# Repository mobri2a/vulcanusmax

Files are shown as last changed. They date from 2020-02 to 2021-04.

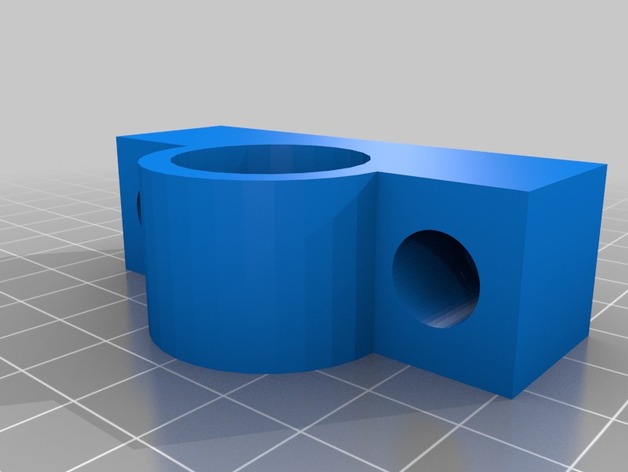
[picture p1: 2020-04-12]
Printed Parts/images/Z_bearing_holder_preview_featured.jpg

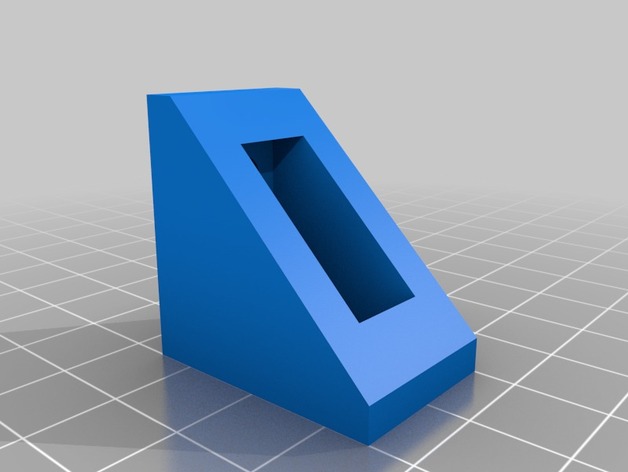
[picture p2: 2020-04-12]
Printed Parts/images/CoreXY_Corner_Bracket_2020_preview_featured.jpg

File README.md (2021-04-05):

# Vulcanus Max

This is the definitive repository for config files for this printer. Firmware is not stored here!

Vulcanus Max is an open source CoreXY, large-capacity printer:
* 2020 extrusion frame
* NEMA 17 stepper motors
	* Kysan 1124090: 1.5A, 4.2V, 1.8 deg
	* Bondtech Extruder
* BigTree Tech SKR v1.4 (LPC1768-based)
* BigTree Tech TFT35 V3.0 Graphic Smart Display Controller https://smile.amazon.com/gp/product/B07VWF4W3J/ref=ppx_yo_dt_b_search_asin_title?ie=UTF8&psc=1
* TMC2209 Drivers
	* Sensorless homing (X&Y)
* BuildTak flexible build plate
* Dual E3D V6 hot ends
* Type 1 thermistor: HT-NTC100K 3950

# Configure and Build Marlin

* Use VSCode. 
* Download latest Marlin, if you so choose.
* Copy latest config from source/Marlin in this repo. 
	* Note: often best to transfer values to new config so as to be up to date on Marlin parameters.

## PINDA Probe Wiring

Connect to Z-MIN. Note: Vulcanus is wired to the Probe and Sensor, which is entirely unnecessary and should be changed to Z-MIN (2/28/21)
bl red green black
+---+
  . | ----- +5V ----- Black -------- Brown
| . | ----- SIG ----- Red   -------- Black 
  . | ----- GND ----- Green -------- Blue 
+---+    

### Pinda wires

* W - not used (temperature sensor on Prusa printers)
* Black - SIG      
* Blue - GND
* Brown - +5V

## Wifi Support

If connecting for the first time, stop looking all over the internet and worrying with that silly BTT Writer. Look at available WiFi SIDs. 

1) Connect to ESP3D. 
2) Go to 192.168.0.1
3) Upload index.html.gz
4) Reboot the printer
5) Go to 192.168.0.1
6) Follow the setup instructions

After initial configuration you'll need to reboot the printer to get the DHCP address from the display. Navigate to that IP and continue setup.

7) Change Station IP Mode to Static
8) Set an IP address (use OctoPi + 1)
9) Set gateway IP
10) Reboot the printer when done and verify static IP address is set

## Embedded WebUI

First time you will need to upload index.html.gz. Get it from https://github.com/luc-github/ESP3D-WEBUI. Use the default UI to upload it, then reboot.

## Notes

**Extruder**: Do not exceed 30mm/s extraction speed. It's a geared extruder and it *does not like it.*

# Build

* Build with PlatformIO. Easiest to output to SD Card

# Install

* Put the MicroSD card from **Build** in the printer and power off/on.
* Reset the EEPROM stored settings: M502, M500, M501

# Operate

## UBL

**Flex Plate**: UBL works very well with the BuildTak flexible build plate system. A script has been configured on Octopi for this purpose.

**Note on Sensorless Probing:** I read that it's not that accurate enough on the Z-axis. TMC2209 on the E0, E1, and Z axis have Stallguard diagnostic pins removed.

Latest: 2/28/21

```
;------------------------------------------
;--- Setup and initial probing commands ---
;------------------------------------------
;M502            ; Reset settings to configuration defaults...
;M500            ; ...and Save to EEPROM. Use this on a new install.
;M501            ; Read back in the saved EEPROM.
M117 UBL Bed Leveling...
M140 S{{ parameters.bedtemp }}          ; Not required, but having the printer at temperature helps accuracy
M109 S{{ parameters.extrudertemp }}     ; Not required, but having the printer at temperature helps accuracy
M190 S{{ parameters.bedtemp }}          ; Wait for the bed (if not already at temperature)

G28             ; Home XYZ.
M155 S30        ; reduce temperature reporting rate
G29 P1 T        ; Do automated probing of the bed.
;G29 P2 B T      ; Manual probing of locations USUALLY NOT NEEDED!!!!
G29 P3 T        ; Repeat until all mesh points are filled in.

#G29 T           ; View the Z compensation values.
G29 S{{ parameters.slot }} ; Save UBL mesh points to EEPROM.
G29 F{{ parameters.fade }}; Set Fade Height for correction at 10.0 mm.
G29 A           ; Activate the UBL System.
@BEDLEVELVISUALIZER     ; tell plugin to watch for reported mesh
M420 S1 V
M500            ; Save current setup. WARNING: UBL will be active at power up, before any `G28`.
;---------------------------------------------
;--- Fine Tuning of the mesh happens below ---
;---------------------------------------------
;G26 C P5.0 F3.0 ; Produce mesh validation pattern with primed nozzle (5mm) and filament diameter 3mm
                ; PLA temperatures are assumed unless you specify, e.g., B 105 H 225 for ABS Plastic
;G29 P4 T        ; Move nozzle to 'bad' areas and fine tune the values if needed
                ; Repeat G26 and G29 P4 T  commands as needed.

;G29 S1          ; Save UBL mesh values to EEPROM.
;M500            ; Resave UBL's state information.
;----------------------------------------------------
;--- Use 3-point probe to transform a stored mesh ---
;----------------------------------------------------
;G29 L1          ; Load the mesh stored in slot 1 (from G29 S1)
;G29 J           ; No size specified on the J option tells G29 to probe the specified 3 points
                ; and tilt the mesh according to what it finds.

M104 S0
M140 S0
M155 S30		; reset temperature keepalive
```

### Setup

#### Do this any time a change is made to the build surface that could change its contour. Run the script above manually, or use the custom command in Octopi.

#### Step 2 - Glass beds

Manually adjust every point on the mesh with a feeler gauge. From the clickwheel, find the menu item to adjust every mesh point. Adjust each to consistent clearance.

#### Step 3

Optional: Get the mesh, load it into Excel, and create a 3D graph of the surface.

1. Copy/paste the mesh data from G29 T
2. Paste into Excel (see file in this repo)
3. Data->Text to columns. Take defaults
4. Delete columns 1 and 3
5. Select data cells and sort by column A (gets rid of blanks and orients graph to match front right view of the bed)
6. Create a 3D Line Chart of the bed measurements

UBL Bed Topology Visualized as an Excel 3D Line Chart

## Bilinear Bed Leveling
### Procedure
1) Preheat for PLA. Heaters (bed and hot end) should remain on. Let the bed fully soak in the heat for a few minutes
2) Use the menu to execute Bed Leveling (I think this is G29)
3) Make sure Bed Leveling is ON

## Adjustments
### Z Offset
* Adjust it before you print
* ...or double-click the knob **during** print and adjust (head adjusts as you turn the knob)
# Contents of this Repo

## source/Marlin

Contains Marlin configs.

### To Update Marlin

* download a zip of the latest Marlin firmware
* Copy the file platformio.ini to the root (same level as Marlin, docs, data, lib, etc)
* Copy the latest configs to the Marlin folder within the downloaded repo
* Build using VSCode

**Note**: It's better to transcribe your config, editing the latest Marlin version to match. Often config directives change between releases. Same for platformio.

Latest build is in Documents/Marlin/Marlin-bugfix-2.0.x, built 4/23/2020. I was attempting to make UBL work properly. It didn't. See open issue on GitHub. Working currently on adding WiFi support.

WiFi is enabled on Serial 1

### See:
* http://www.github.com/codiac2600

## Cura

All files needed to install the printer into Cura

## Other

printer_init.gcode - sets up the unified bed leveling mesh

# Specifications

https://mak3r.de/2020/04/03/stepper-driver-current-and-vref-calculator/

## X Axis

Stepper motor: Kysan 1124090 Nema 17
2 Phase
1.8 angle
2.8ohm / phase
1.5A / phase
5mm

RMS = 1.5 / 1.41 = 1.064
Vref = (1.064 * 2.5) / 1.77 = 1.502
90% = 1.5 = 958mA

Driver: TMC2209 in UART mode with StallGuard

Pulley: GT2 20 tooth

Belt pitch: 2mm

## Y Axis

Stepper motor: Kysan 1124090 Nema 17
2 Phase
1.8 angle
2.8ohm / phase
1.5A / phase
5mm

RMS = 1.5 / 1.41 = 1.064
Vref = (1.064 * 2.5) / 1.77 = 1.502
90% = 1.5 = 958mA

Driver: TMC2209 in UART mode with StallGuard

Pulley: GT2 20 tooth

Belt pitch: 2mm

## Z Axis

Stepper motor: Kysan 1124090 Nema 17 (2)
2 Phase
1.8 angle
2.8ohm / phase
1.5A / phase
5mm

RMS = 2 * 1.5 / 1.41 = 2.128
Vref = (2.128 * 2.5) / 1.77 = 3.006
90% = 1.9152 = 1915mA

RMS: Conservatively set X_CURRENT to 1500 (2/28/21)

Driver: TMC2209 in UART mode

Min Z Probe: 18mm inductive

Lead screw: 8mm

## Extruder 1

Stepper motor: Bondtech 42H025H-0704-002 25mm NEMA 17 0.7A, 2.9V, 1.8 deg
2 Phase
1.8 angle
4.2ohm / phase
0.7A / phase
2.9V / phase

Driver: TMC2209 in UART mode

RMS = 0.7 / 1.41 = 0.496
Vref = (0.496 * 2.5) / 1.77 = 0.700 V
90% = 0.496 = 446mA

## VREF Calculation

RMS current = Max current / 1.41
Vref = (RMS Current x 2.5) / 1.77
Use 90% of RMS current

----- old stuff----
# Vulcanus Max
## Overview

This project is to create a large-format 300x300x400mm Fused Deposit Modelling (FDM) printer based on CoreXY design using the 2015 Vulcanus Max project as a starting point.

## Configure and Build Marlin

1) Download BTT Marlin 2.0.x bugfix
2) Download latest 2.0 Marlin
3) Copy #2 over #1
4) Copy platformio.ini to root of #1 over the exiting platformio.ini
5) Edit the config files in #1 and transfer settings from latest build/Marlin in this repo

### Specific Config Changes

#### configuration.h

Numerous (to be listed)

```
#define STRING_CONFIG_H_AUTHOR "(Elvantech, SKR-V1.4 LPC1768)"
#define SERIAL_PORT 3
#define SERIAL_PORT -1
#define BAUDRATE 115200
#define MOTHERBOARD BOARD_BTT_SKR_V1_4
#define CUSTOM_MACHINE_NAME "Vulcanus SKR"
#define REPRAP_DISCOUNT_FULL_GRAPHIC_SMART_CONTROLLER
#define NEOPIXEL_LED
  #define NEOPIXEL_TYPE   NEO_GRB 
  #define NEOPIXEL_PIN     P1_24  
  #define NEOPIXEL_PIXELS 26    
  #define NEOPIXEL_STARTUP_TEST 
```
Preheats
```
#define PREHEAT_1_LABEL       "PLA"
#define PREHEAT_1_TEMP_HOTEND 210
#define PREHEAT_1_TEMP_BED     60
#define PREHEAT_1_FAN_SPEED     0 // Value from 0 to 255

#define PREHEAT_2_LABEL       "ABS"
#define PREHEAT_2_TEMP_HOTEND 245
#define PREHEAT_2_TEMP_BED    105
#define PREHEAT_2_FAN_SPEED     0 // Value from 0 to 255

#define PREHEAT_3_LABEL       "Nylon"
#define PREHEAT_3_TEMP_HOTEND 245
#define PREHEAT_3_TEMP_BED     80
#define PREHEAT_3_FAN_SPEED     0 // Value from 0 to 255

#define PREHEAT_4_LABEL       "PETG"
#define PREHEAT_4_TEMP_HOTEND 230
#define PREHEAT_4_TEMP_BED     70
#define PREHEAT_4_FAN_SPEED     0 // Value from 0 to 255

#define PREHEAT_5_LABEL       "TPU"
#define PREHEAT_5_TEMP_HOTEND 200
#define PREHEAT_5_TEMP_BED     90
#define PREHEAT_5_FAN_SPEED     0 // Value from 0 to 255
```

#### configuration_adv.h

X_CURRENT = 1000
Y_CURRENT = 1000
Z_CURRENT = 1000

#### configuration_secure.h

Just copy it.

## Objectives

### Features

* Remote printing

Use OctoPrint to print over WiFi. The built-in camera lets you monitor your print. OctoPrint allows you to remotely control the printer.

* Heated Bed

The build surface can use the Monoprice 300x300 flexible build plate or borosilicate glass plate. Autoleveling makes print setup easier.

* Zoned Heated Bed

The 300x300mm heated bed has 3 zones, small, medium, or large, to reduce power consumption by only heating the portion of the bed that is needed based on the footprint of the model.

* Controller

32 bit processor running at 120MHz with 2209 stepper motor drivers and Marlin 2.0 firmware.

* Extruders

Dual Bowden tube extruders minimize print head mass for less vibration and faster print head movement.

* Vibration-free Frame

Dampers are used on all moving parts to reduce vibration.

* Ambient Temperature Management

Insulated side panels and an exhaust fan allow control of the ambient temperature inside the printer. A heater brings the enclosure quickly up to temperature before your print starts.

* Safety

High amperage power is isolated and protected so that an electrical fault will not cause a fire or damage to the controller.

## Design

### Frame

### Lighting

### Gantry

### Heated Bed

### Print Head

#### Hot Ends

#### Extruders

### Controller

32 bit BIGTREETECH

#### Firmware

Marlin 2.0

### Power

## Bill of Materials

| Item | Qty | Cost |
| -- | :--: | --: |
| [BIGTREETECH TMC2209 V1.2 Stepper Motor Drivers](https://www.aliexpress.com/snapshot/0.html?productId=33029587820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)| 5 | $28.88 |
| [BIGTREETECH SKR V1.4 Turbo Control Board](https://www.aliexpress.com/snapshot/0.html?productId=4000480059509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)| 1 | $33.00 |
| Stepper Motors | | |
| 2020 Extrusion | | |
| Display panel | | |
| Extruder | | |
| Hot End | | |

## Printed Parts

## References

### Similar projects

* [Vulcanus MAX](https://www.instructables.com/id/Vulcanus-MAX-CoreXY-Aluminum-Frame-RepRap-3D-Print/)
* [Vulcanus V1](https://www.instructables.com/id/Vulcanus-V1-3D-Printer/)

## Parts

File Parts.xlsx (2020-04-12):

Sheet: Sheet1
2020 Extrusion | https://www.aliexpress.com/item/32859762475.html
2020 Extrusion | https://www.aliexpress.com/item/32918828145.html

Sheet: Budget
Part | Description/Notes | Qty | Budget | Actual | Link/Order

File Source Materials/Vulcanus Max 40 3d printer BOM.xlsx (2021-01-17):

Qty | Part Name/Type | Source | Source Qty | Source Price
 | FRAME |  |  |  | ordered 3/30 | Status
4 | 20x20 Aluminum Extrusion - 700mm - 5537T101 | https://folgertech.com/products/2020-20mm-x-20mm-x-1meter-extruded-alumium-beam-for-kossel-diy-projects | 4 | $30.33 total | aliexpress
16 | 20x20 Aluminum Extrusion - 590mm length |  | 10 @ 1200 |  | banggood
2 | 20x20 Aluminum Extrusion - 505mm length
2 | 20x20 Aluminum Extrusion - 460mm length
1 | 20x20 Aluminum Extrustion - 600mm | for x carriage | 1 | $12.95 | aliexpress | Received
1 | 20x20 Aluminum Extrusion - 590mm length - x carriage (NEW)
 | 24 pieces @ 1meter long |  | Total | $107.76 + 40.35 shipping
4 | 12mm smooth rods - 541mm length | http://www.ebay.com/itm/162021393198?var=460991532709 | 4 | $16.57 + $5.57 shipping | aliexpress | Reordered | 2020-06-27
 | Replaced with linear rails for x and y axis
4 | Linear rails 600mm | https://www.aliexpress.com/item/33013832781.html |  | $22.73 | aliexpress
2 | 10mm smooth rods - 537mm length | http://www.ebay.com/itm/152032174444?var=451230323416 | 4 pcs @ 600mm | $16.83 | aliexpress | Received
2 | 10mm smooth rods - 511mm length |  |  |  |  | Received
160 | M5 extrusion nuts | https://folgertech.com/products/12-x-lm8uu-4-x-608zz-2-x-623zz-bearing-kit-prusa-i3-rework-reprap-3d-printer | 100pcs | $12.99 + shipping | banggood | received
120 | M5 - 10mm screws | http://www.ebay.com/itm/262320320195?var=561086661523 | 50 pcs | $4.19 | banggood | out of stock
30 | M5 - 12mm screws | http://www.ebay.com/itm/262320320195?var=561086661523 | 50 | $4.39 | banggood | out of stock
8 | M5 - 25mm screws | http://www.ebay.com/itm/262320320195?var=561086661523 | 10 | $3.99 | banggood | out of stock
2 | M8 screw rods - 31.5cm -400m stock with brass nut | https://folgertech.com/products/400mm-lead-screw-3d-printer-z-axis-lead-screw-acme-lead-screw-8mm-screw-pitch | 1 | $15.99 | aliexpress |  |  | order running late - reordering
100 | M4 square nuts | http://www.ebay.com/itm/262161161642?var=560925921904 | 100 | $8.49 | aliexpress
100 | M4 screw - 6mm | http://www.ebay.com/itm/Metric-M3-M4-Black-10-9-Alloy-Steel-Button-Head-Hex-Socket-Cap-Screw-Bolt-/222066527965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 | 50 | $2.65 | aliexpress
 | m4 hex nuts | http://www.ebay.com/itm/131660048805?var=431050278100 | 50 | $2.65
8 | LM10UU linear bearings | https://folgertech.com/products/10x-lm10uu-linear-bearing | 8 | 2 for $3.68 | aliexpress
4 | LMK12L linear bearings | http://www.ebay.com/itm/162014356405 | 1 | $7.82 for 2 + $3.23 shipping | aliexpress | Reordered | 44009
 | Replaced with linear rails for x and y axis
17 | 624 bearings | http://www.ebay.com/itm/310578391085 | 5pcs | 4 @ $13.80 | aliexpress
2 + 2 | GT2 pulleys and belts | http://www.ebay.com/itm/291658850152 | 8 + 5 | $11.92 + $2.99 shipping | banggood
1 | MK8 Direct Drive Gear for Extruder | http://www.ebay.com/itm/201531284546 | 2 | $5.99
2 | M8 threaded rod - 31.5cm length | http://www.ebay.com/itm/322101241224?var=511026880397 | 1 | $8.59 + $1.85
2 | Z axis 5mm to 8mm coupler | http://www.ebay.com/itm/221500601581 | 2 | $3.96 | banggood | received
1 | 5mm x 500mm x 500mm aluminum plate |  |  |  |  | redesign - I don't like how the Vulcanus uses a 5mm plate to support a 5mm plate
1 | 5mm x 400mm x 400mm aluminum plate |  |  |  | aliexpress | received
 | 8mm anti-backlash spring-loaded nut |  | 2 | 2.29 | banggood | out of stock
 | ELECTRONICS
5 | Nema 17 Stepper Motor Bipolar | http://www.ebay.com/itm/231427537485 | 5 | $58.00
1 | Ramps 1.4 kit w/Arduino Mega 2560 & LCD, stepper motor drivers | http://www.ebay.com/itm/321977486681 | 1 | $39.90 + $3.58 shipping | N/A
1 | E3D V6 hotend 1.75mm | https://www.matterhackers.com/store/printer-accessories/v6-hotend-full-kit-1.75mm-universal | 1 | $78.00 | N/A
3 | Scythe Mini KAZE ULTRA 40mm Silent Mini Fan | http://www.ebay.com/itm/162119217575 | 1 | $6.09 | banggood | received
2 | SilenX EFX-08-12 80mm Effizio Quiet Case Fan | http://www.ebay.com/itm/291286908487 | 1 | $8.99 | banggood
1 | 40cm x 40cm 600W 110V Silicone Heater Pad | http://de.aliexpress.com/item/Silicone-Heating-Pad-Heater-110V-600W-400-400mm-for-3d-printer-heat-bed/32639533112.html | 1 | $32 + $21.08 | banggood | received
1 | EVGA 210-GQ-1000-V1 1000W ATX12V / EPS12V Power Supply | http://www.newegg.com/Product/Product.aspx?item=N82E16817438062 | 1 | $129.99 |  | Need to figure out power needs. Would like to use 24V PS
5 | TMC2209 stepper driver |  |  |  | banggood | out of stock
 |  |  | ebay total | $301.85
 |  |  | Folgertech | $215.92
 |  |  | matter hackers | $78.00
 |  |  | ali express | $53.08
 |  |  | newegg | $129.99
 |  |  | TOTAL as of 8/3/16 | $778.84
 |  |  | KEY:
 |  |  | Needs update
 |  |  | Purchased

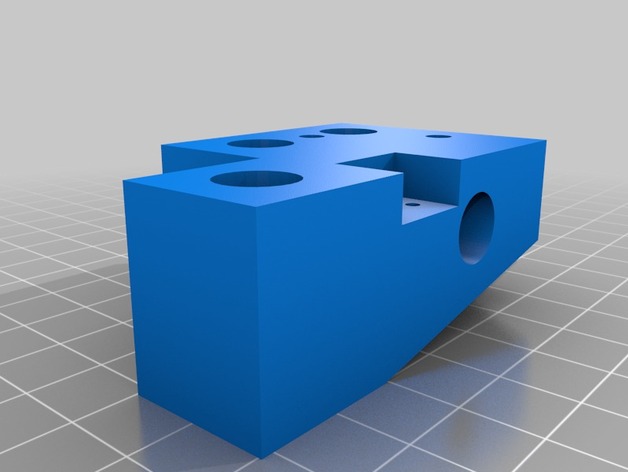
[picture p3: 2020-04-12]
Printed Parts/images/YidlerRight_preview_featured.jpg

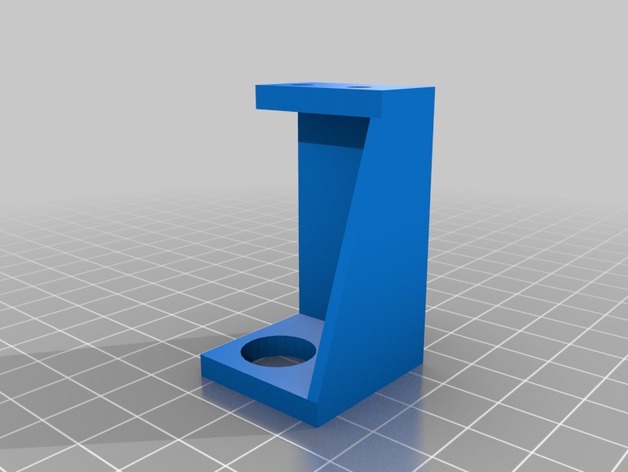
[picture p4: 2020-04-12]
Printed Parts/images/05fd83058f6de9fed415d9ea554de397_preview_featured.jpg

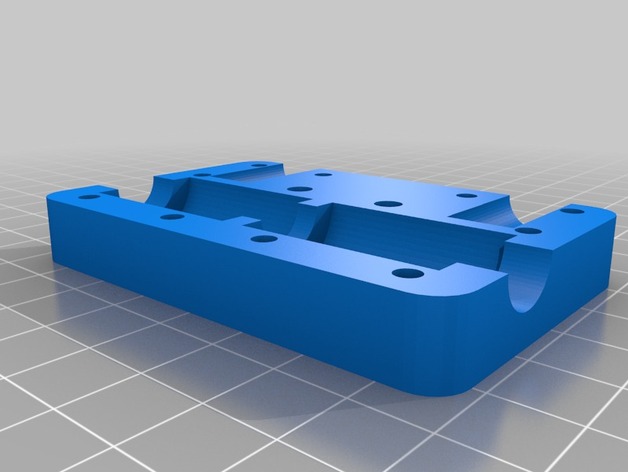
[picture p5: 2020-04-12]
Printed Parts/images/XRightdown_preview_featured.jpg

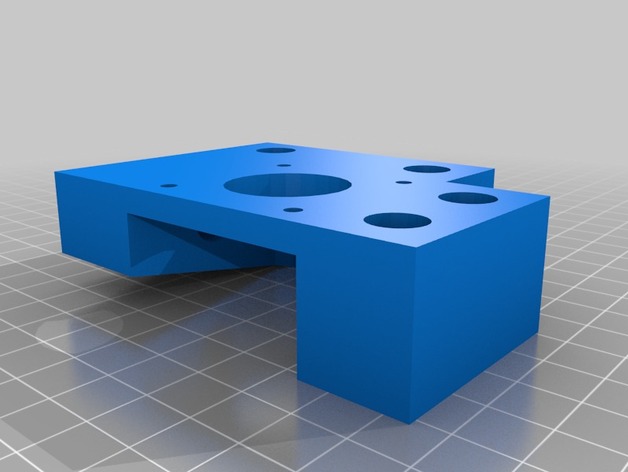
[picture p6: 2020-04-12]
Printed Parts/images/e0d60139beee853cb4de93a20eb8b1da_preview_featured.jpg

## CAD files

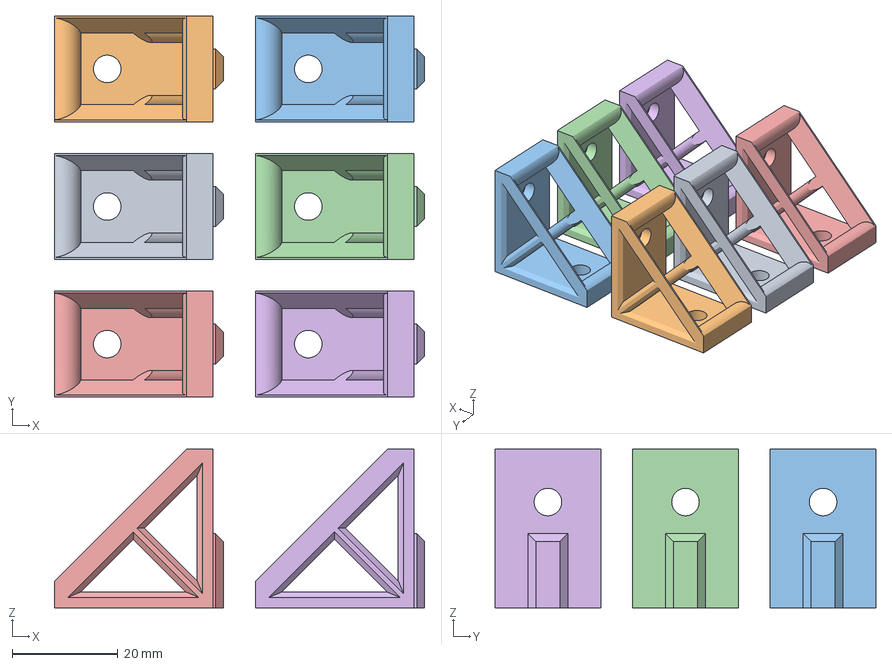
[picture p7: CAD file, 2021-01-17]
Printed Parts/files/corner-bracket-ebt.3mf
70.0 x 72.0 x 30.0 mm

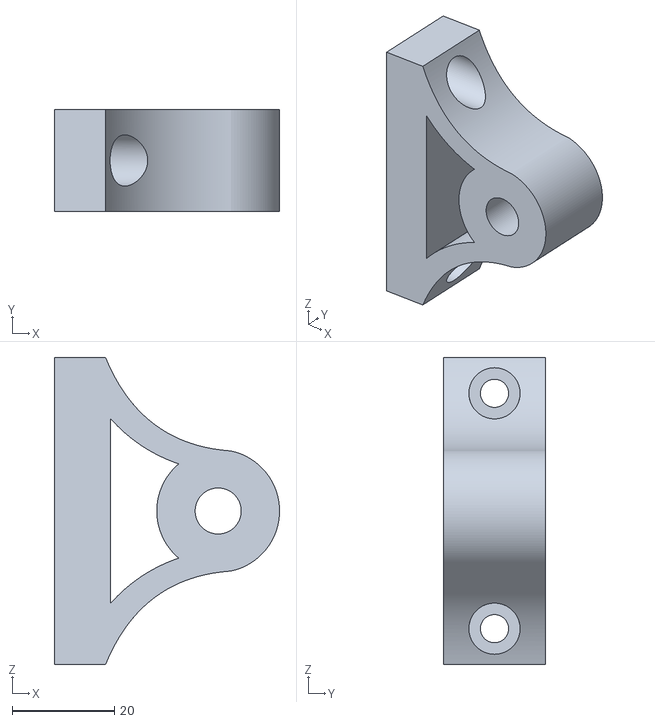
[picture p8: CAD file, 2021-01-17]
Printed Parts/files/z-block-ebt.stl
44.0 x 20.0 x 60.0

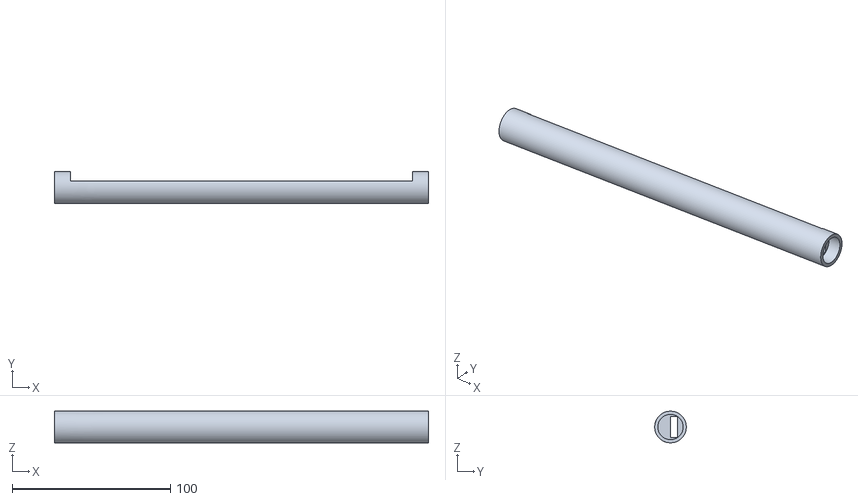
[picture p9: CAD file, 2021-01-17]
Printed Parts/files/lightbar.stl
236.0 x 20.0 x 20.0

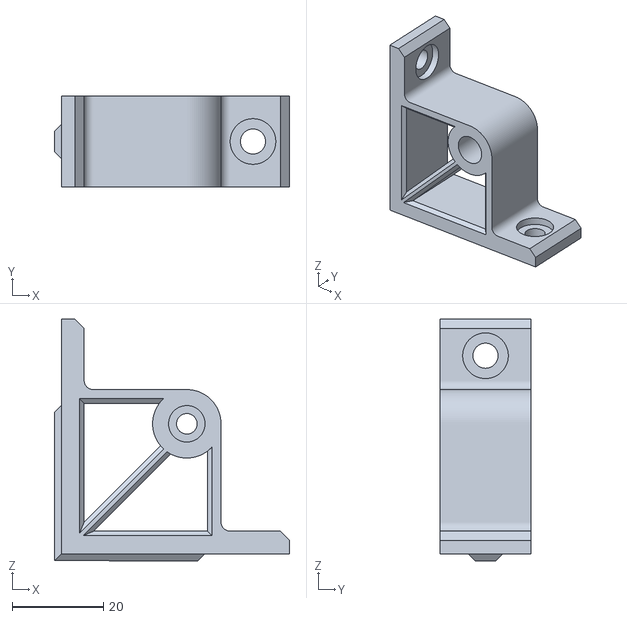
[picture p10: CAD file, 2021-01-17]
Printed Parts/files/bed corner 1.stl
51.5 x 20.0 x 52.9

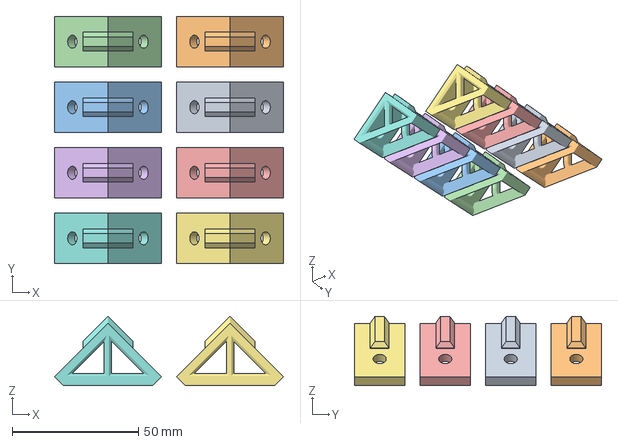
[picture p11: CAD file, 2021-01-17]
Printed Parts/files/corner-bracket-ebtx8.3mf
90.9 x 98.0 x 27.6 mm

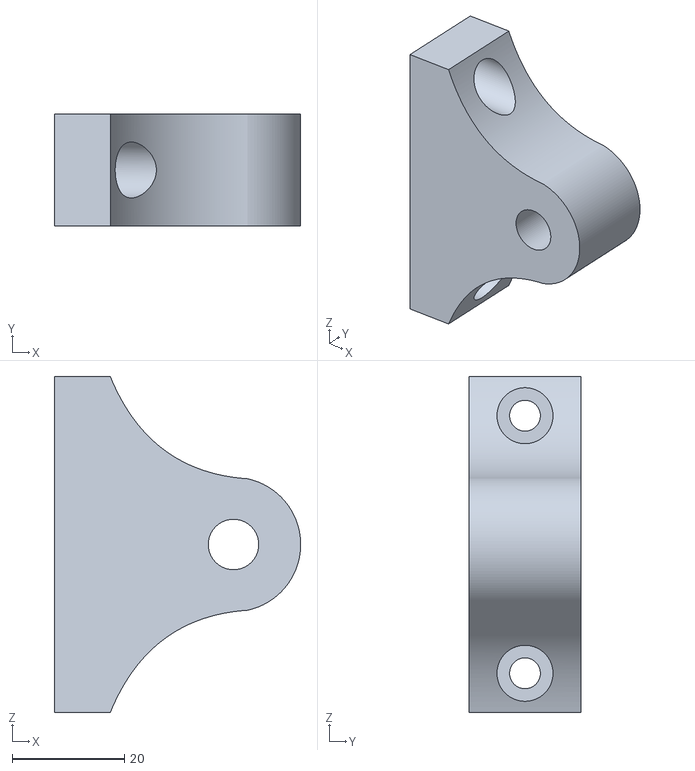
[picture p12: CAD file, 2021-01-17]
Printed Parts/files/z-axis-vm.stl
44.0 x 20.0 x 60.0

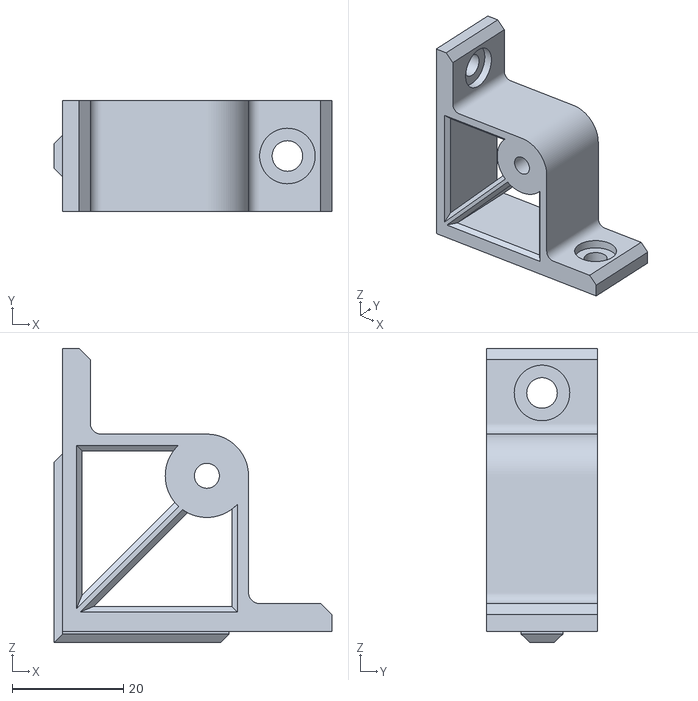
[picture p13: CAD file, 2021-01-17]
Printed Parts/files/bed corner 2.stl
50.0 x 20.0 x 52.9

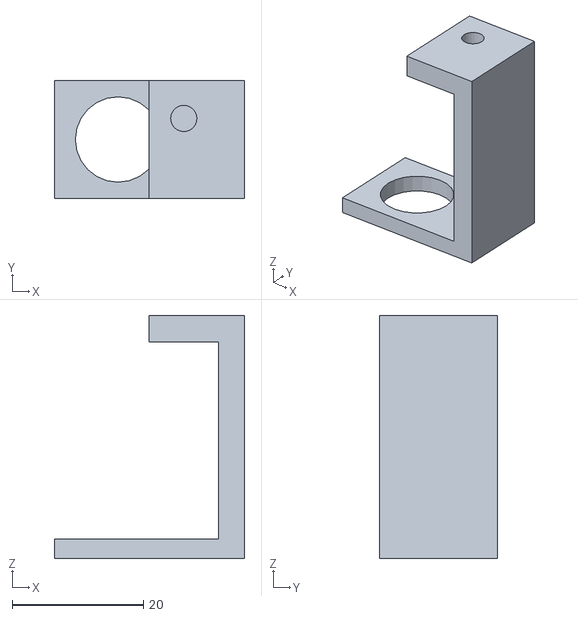
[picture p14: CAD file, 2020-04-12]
Printed Parts/files/Inductive_sensor_holder_fixed.stl
29.0 x 18.0 x 37.0

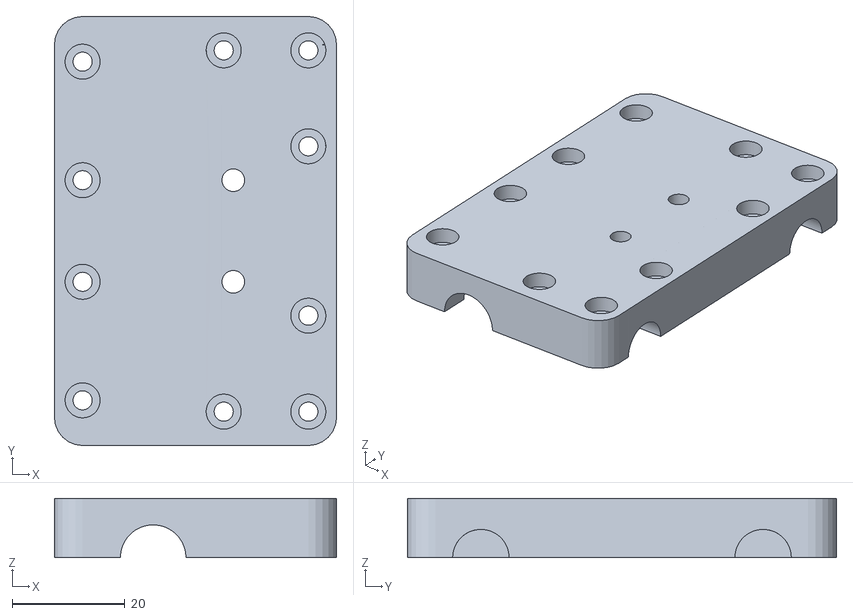
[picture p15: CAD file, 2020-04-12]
Printed Parts/files/XRightUP.stl
50.0 x 76.0 x 10.5

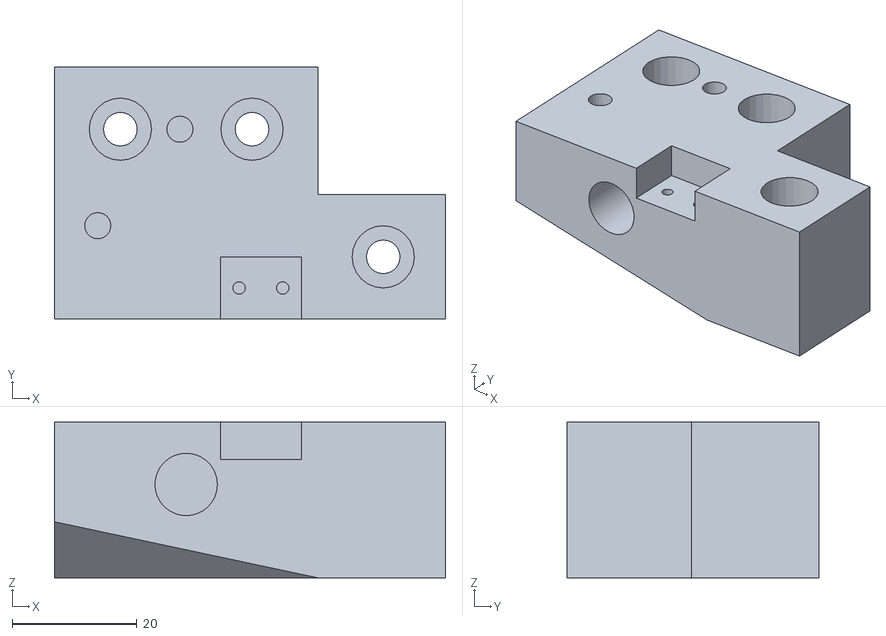
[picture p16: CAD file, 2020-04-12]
Printed Parts/files/YIdlerLeft.stl
62.8 x 40.5 x 25.0

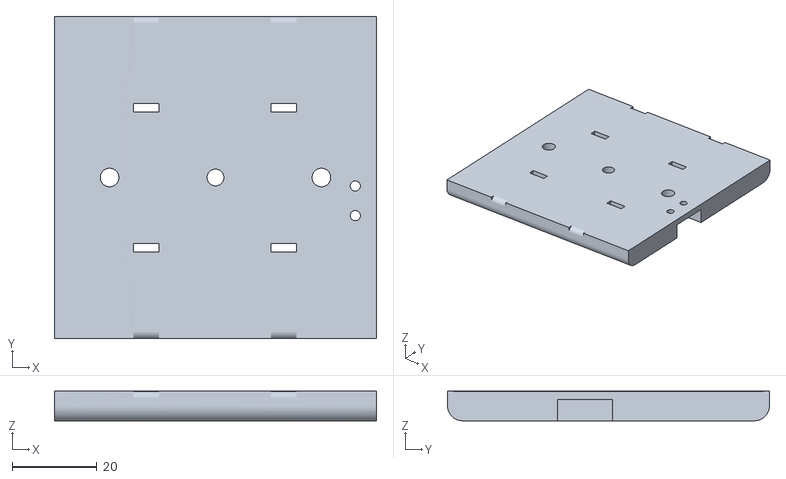
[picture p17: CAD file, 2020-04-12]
Printed Parts/files/xycarridge_fixed.stl
76.0 x 76.0 x 7.00

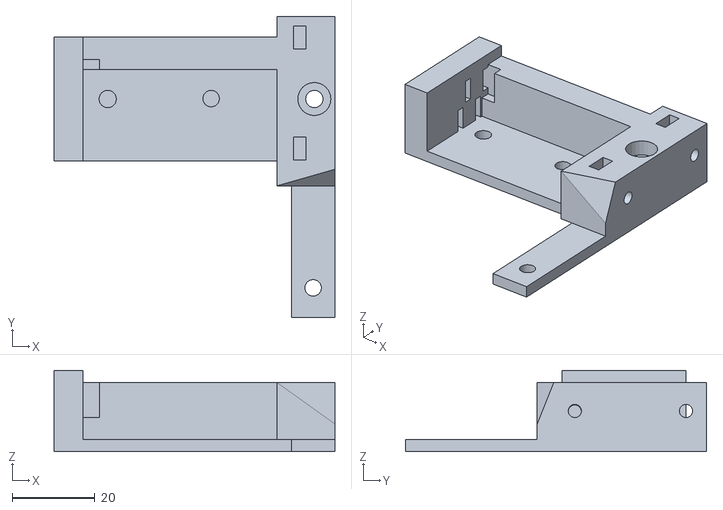
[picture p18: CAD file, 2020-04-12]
Printed Parts/files/vulcanusdirect_fixed1.stl
68.0 x 72.9 x 19.7

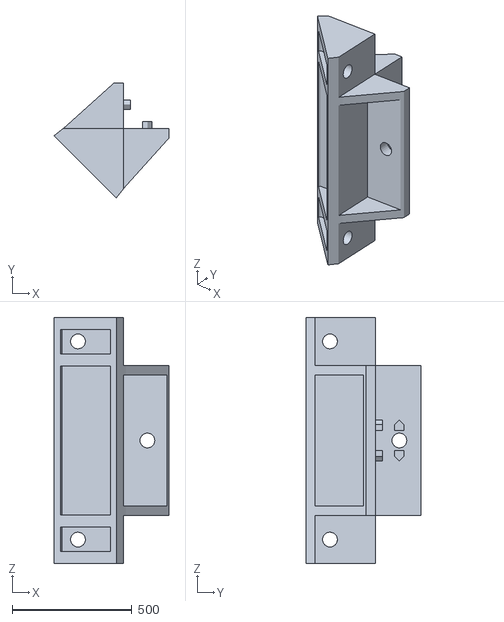
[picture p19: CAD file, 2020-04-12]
Printed Parts/files/cantos_juntos_final_2017_repaired.stl
480.0 x 480.0 x 1027.8

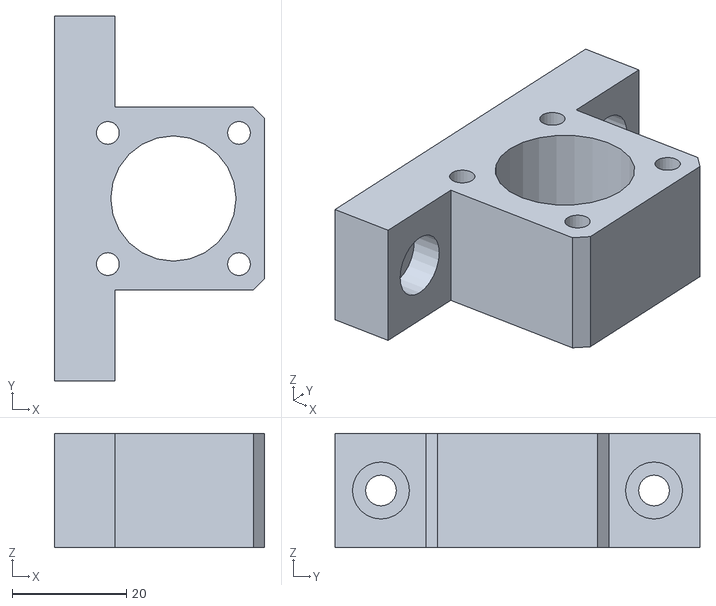
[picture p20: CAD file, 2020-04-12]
Printed Parts/files/Z_Axis_bearing_holder.stl
36.9 x 64.0 x 20.0

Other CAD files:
Printed Parts/files/XRightdown.stl
Printed Parts/files/CoreXY_Corner_Bracket_2020.stl
Printed Parts/files/VMAXNEW__Y_MOTOR_MOUNT_2016_repaired.stl
Printed Parts/files/Xleftdown.stl
Printed Parts/files/12RODBIGBLOCK.stl
Printed Parts/files/12RODSMALLBLOCK.stl
Printed Parts/files/CoreXY_Belt_tensioner.stl
Printed Parts/files/VMAX_20_20_Profile_Cornner_03_03.stl
Printed Parts/files/VMAX_MOTOR_MOUNT.stl
Printed Parts/files/Xleftup.stl
Printed Parts/files/YidlerRight.stl
Printed Parts/files/YmotorLeft.stl
Printed Parts/files/YmotorRight.stl
Printed Parts/files/Z_M8_nut.stl
Printed Parts/files/Z_bearing_holder.stl
Printed Parts/files/corner-bracket-ebt.stl
Printed Parts/files/diamond_hotend_adaptor_vmax_.stl
Printed Parts/files/inducao_reforcado.stl
Printed Parts/files/mk8_reforcado__fixed.stl
Printed Parts/files/mk8_reforcado__repaired.stl
Printed Parts/files/zmotormount.stl

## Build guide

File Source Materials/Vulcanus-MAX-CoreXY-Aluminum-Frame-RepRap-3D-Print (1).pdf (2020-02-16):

http://www.instructables.com/id/Vulcanus-MAX-CoreXY-Aluminum-Frame-RepRap-3D-Print/technology (http://www.instructables.com/tag/type-id/category-technology/) workshop (http://www.instructables.com/tag/type-id/category-workshop/) craft (http://www.instructables.com/tag/type-id/category-craft/) home (http://www.instructables.com/tag/type-id/category-home/) food (http://www.instructables.com/tag/type-id/category-food/) play (http://www.instructables.com/tag/type-id/category-play/) outside (http://www.instructables.com/tag/type-id/category-outside/) costumes (http://www.instructables.com/tag/type-id/category-costumes/)

# Vulcanus MAX - CoreXY Aluminum Frame 3D Printer Scale UP

by aldricnegrier (http://www.instructables.com/member/aldricnegrier/?utm_source=pdf&utm_campaign=title) on September 21, 2015

Table of Contents

Author:aldricnegrier www.reprapalgarve.com Aldric Negrier

## Intro: Vulcanus MAX - CoreXY Aluminum Frame 3D Printer Scale UP

On May 11, 2015 vulaman published the Vulcanus V1 (http://www.instructables.com/id/Vulcanus-V1-3D-Printer/) 3D printer on his instructables channel. Coincidentally reprapalgarve was working on a coreXY project and when we saw Vulcanus V1 we immediately jumped on to the wagon.

With the experience we had scaling up the Prusa i3 (called Mega Prusa i3) we redesigned the Vulcanus V1 parts in order to allow 32x32x32, 42x42x42 and 52x52x52 (this last version still untested).

The Vulcanus Max 30 has a 32x32x32 build volume, E3D V6 lite extruder, auto bed leveling and MK8 Direct Drive system.

The Vulcanus Max 40 has a 42x42x42 build volume, E3D V6 lite extruder, auto bed leveling and MK8 Direct Drive system.

In summary, Vulcanus Max is a scaled up version of Vulcanus V1 with some upgrades, all metal direct drive, auto-bed leveling, LM10UU bearings and LMH12UU Z bearings and colorful acrylic panels.

Have a look at the video of the V MAX in action at the Maker Faire Lisbon 2015:

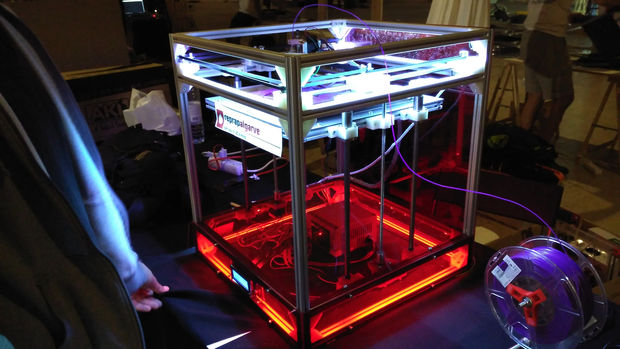
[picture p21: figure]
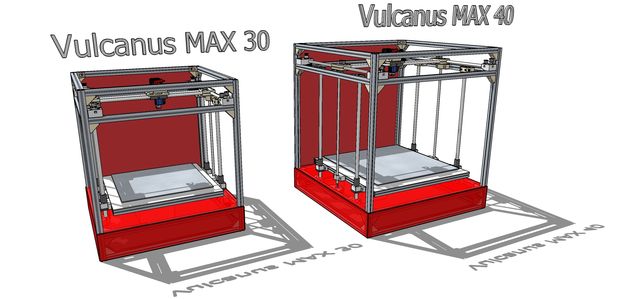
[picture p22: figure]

## Step 1: Open Design - Vulcanus Max 30 and Vulcanus Max 40

A RepRap 3D printer is always open design so please feel free to download the sketchup file. All dimensions are in 1 to 1 scale.

There are 2 versions we have tested, and are working 100%. Vulcanus MAX 30 and Vulcanus MAX 40, we am still working on the Vulcanus MEGA MAX (52x52x150) so keep tuned in.

Use the sketchup for dimensions, and the Vulcanus V1 instructions to guide our way through the build process.

http://www.instructables.com/id/Vulcanus-V1-3D-Printer/

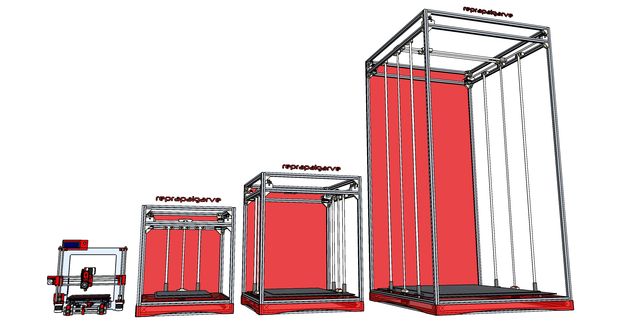
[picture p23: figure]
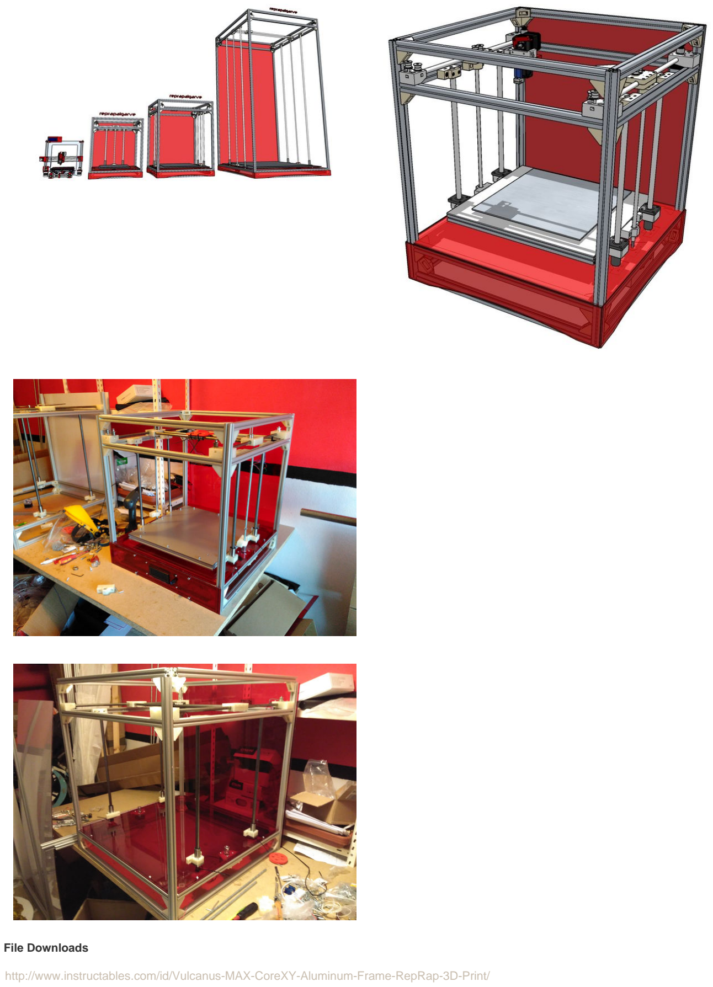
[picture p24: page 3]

File Downloads vulcanus_max.skp (http://www.instructables.com/files/orig/FU9/O6P0/IF4IGBMU/FU9O6P0IF4IGBMU.skp) (25 MB)
[NOTE: When saving, if you see .tmp as the file ext, rename it to 'vulcanus_max.skp'] (http://www.instructables.com/files/orig/FU9/O6P0/IF4IGBMU/FU9O6P0IF4IGBMU.skp)

## Step 2: List of Diferent Parts from Vulcanus V1

Vulcanus Max 30 and 40 are upscale from Vulcanus V1 3D printer, so most of the parts are different:

- Z smooth rods are 12mm instead of 8mm (for rigidity).
- XY smooth rods are 10mm instead of 8mm (for rigidity).
- XY bearings are LM10UU instead of LM8UU.
- Z bearings are LMH12UU instead of LM8UU.
- Extruder is MK8 Direct Drive instead of original Vulcanus V1 extruder.
- All parts where redesigned to allow bigger bearings and bigger rods, with the exception of the corners and the Z motor holders.
- The aluminum print plate is 5mm thick.
- Red acrylic panels instead of metal ones.
- LED strip on top and in the bottom of the second base.
- The V MAX's use inductive sensors for autobed leveling.
- Using repetier firmware instead of Marlin firmware (because i am more used to repetier).

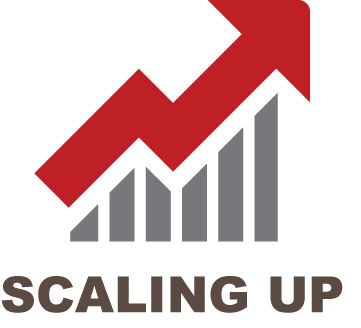
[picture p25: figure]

## Step 3: XY Axis Parts - CORE XY

The original parts where redesigned to fit 10mm smooth rods and LM10UU bearings.

You will need 2 Yidlers parts, 1 normal 1 mirrored:

You will need 2 Ymotors parts, 1 normal 1 mirrored:

You will need 2 Xdown parts, 1 normal 1 mirrored:

You will need 2 Xup parts, 1 normal 1 mirrored:

## Step 4: Z Axis Parts

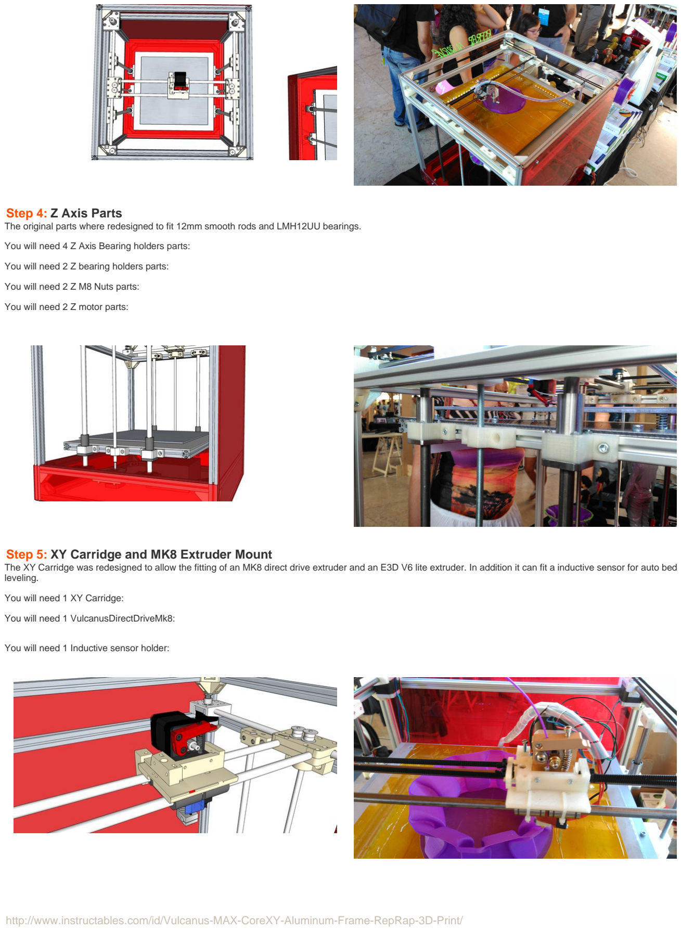
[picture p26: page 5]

The original parts where redesigned to fit 12mm smooth rods and LMH12UU bearings.

You will need 4 Z Axis Bearing holders parts:

You will need 2 Z bearing holders parts:

You will need 2 Z M8 Nuts parts:

You will need 2 Z motor parts:

## Step 5: XY Carridge and MK8 Extruder Mount

The XY Carridge was redesigned to allow the fitting of an MK8 direct drive extruder and an E3D V6 lite extruder. In addition it can fit a inductive sensor for auto bed leveling.

You will need 1 XY Carridge:

You will need 1 VulcanusDirectDriveMk8:

You will need 1 Inductive sensor holder:

## Step 6: Some 3d Printed parts

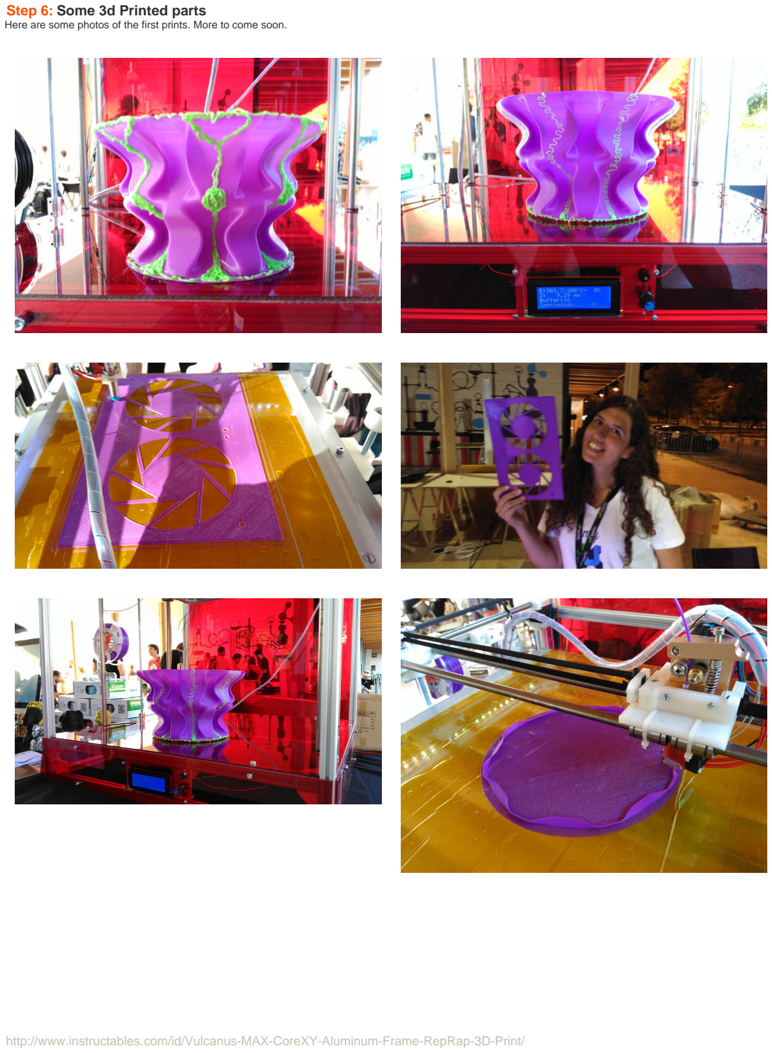
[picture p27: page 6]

Here are some photos of the first prints. More to come soon.

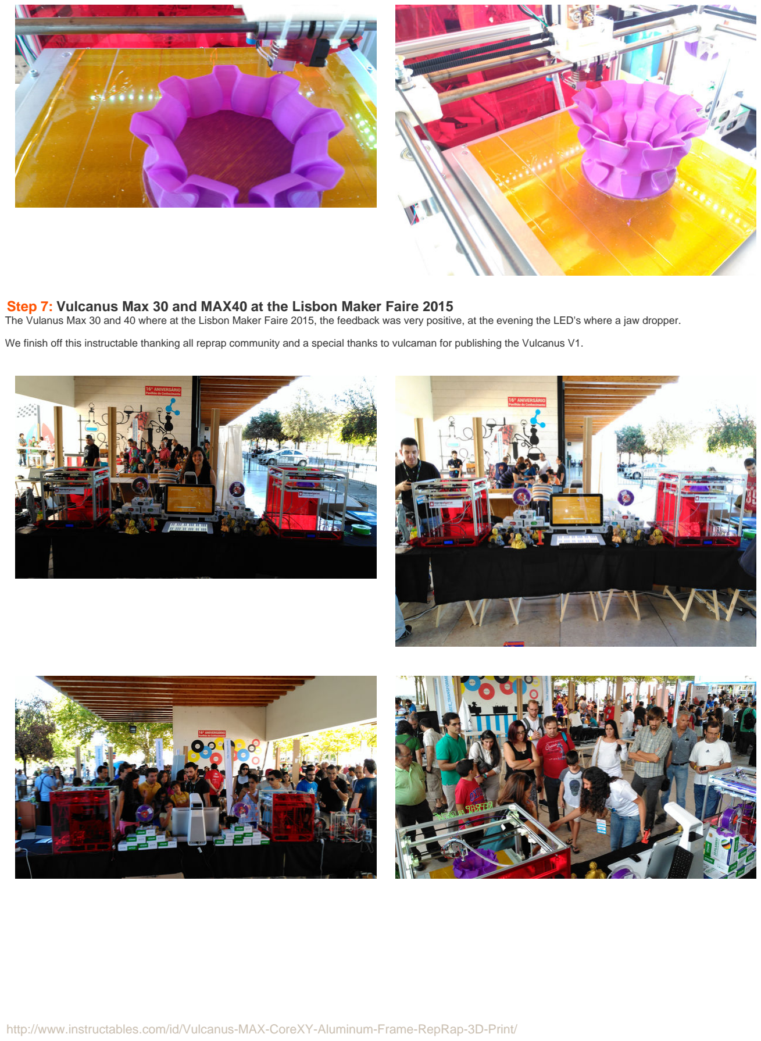
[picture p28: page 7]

## Step 7: Vulcanus Max 30 and MAX40 at the Lisbon Maker Faire 2015

The Vulanus Max 30 and 40 where at the Lisbon Maker Faire 2015, the feedback was very positive, at the evening the LED's where a jaw dropper.

We finish off this instructable thanking all reprap community and a special thanks to vulcaman for publishing the Vulcanus V1.

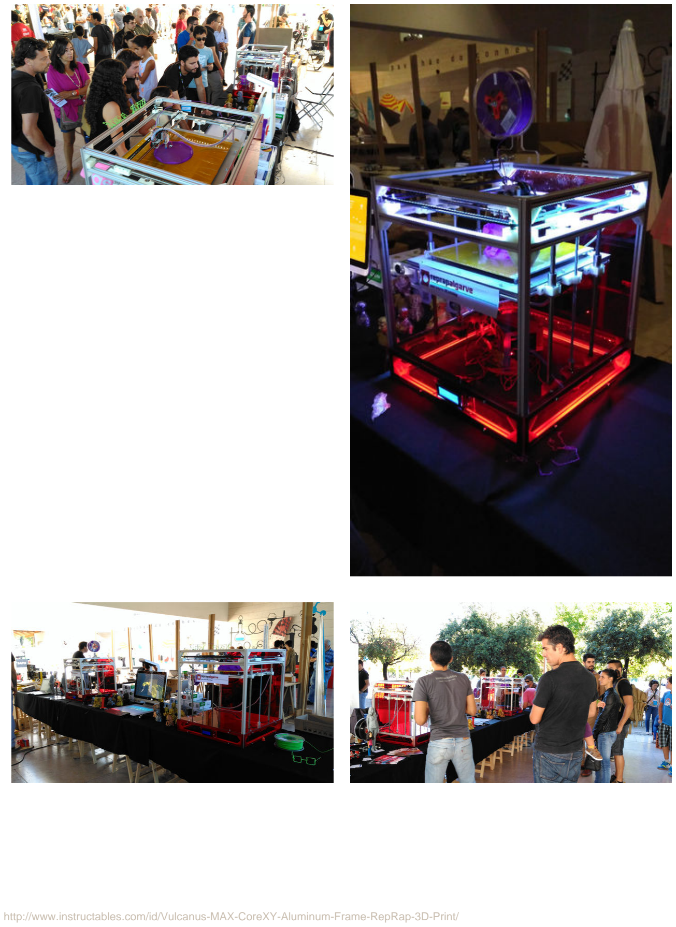
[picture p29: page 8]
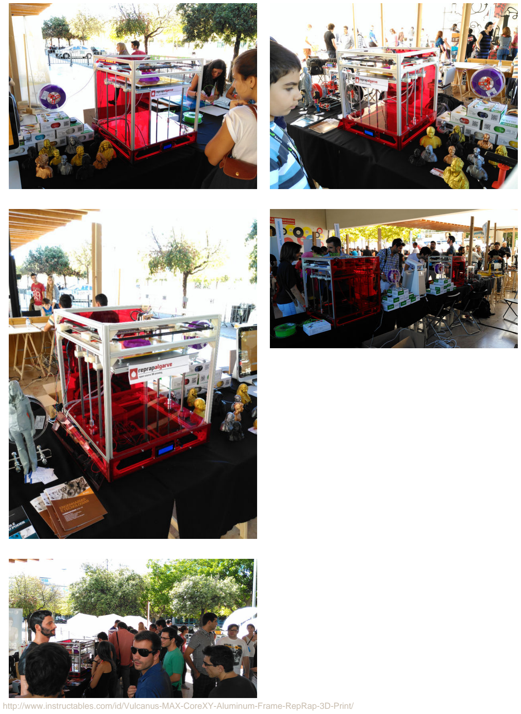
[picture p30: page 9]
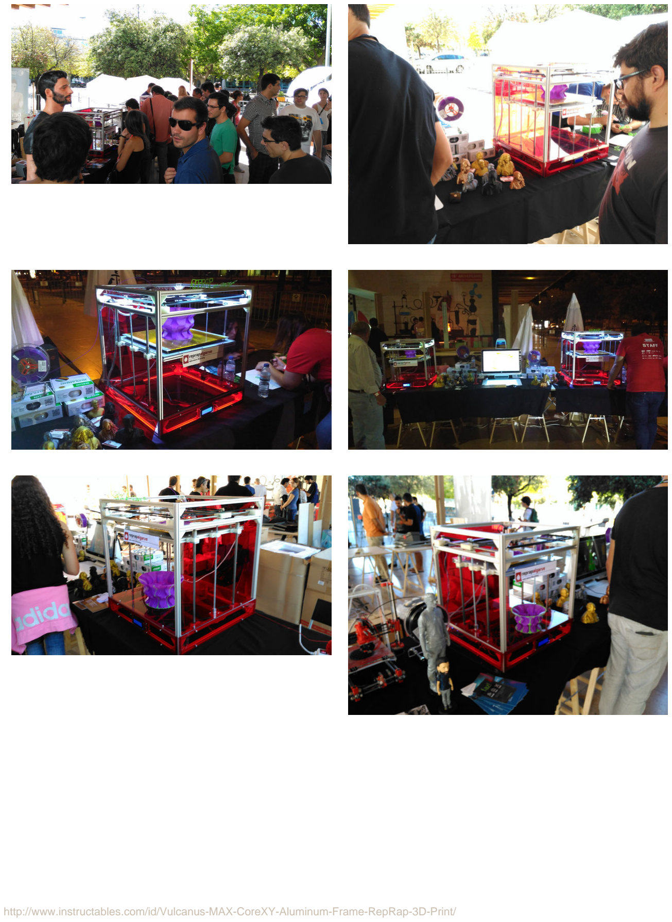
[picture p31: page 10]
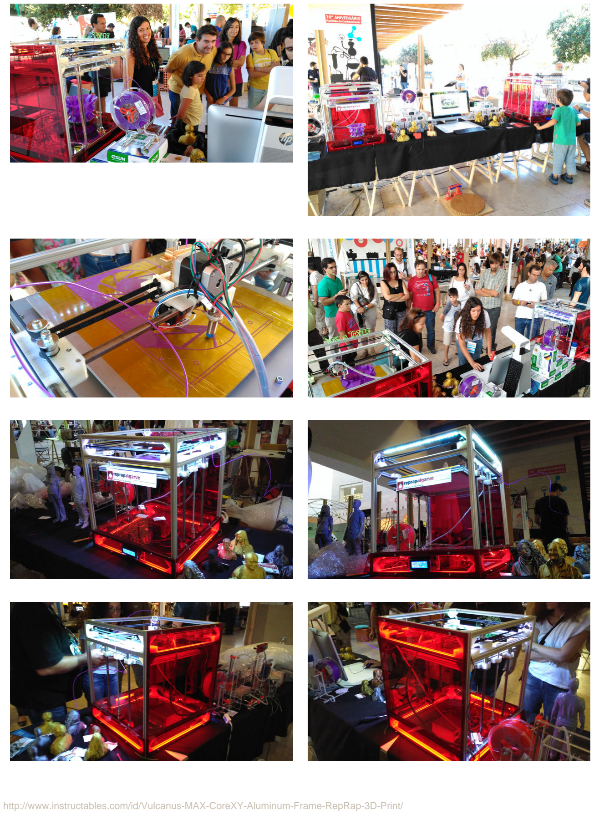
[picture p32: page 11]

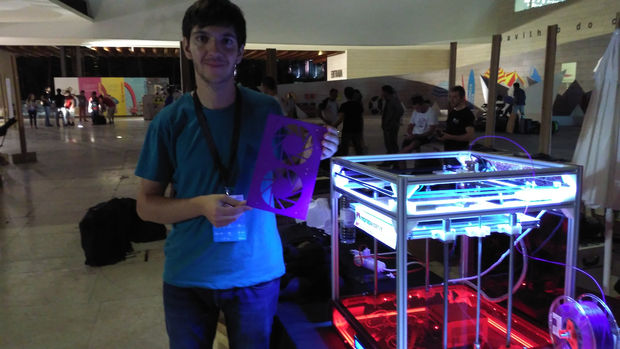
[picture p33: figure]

## Related Instructables

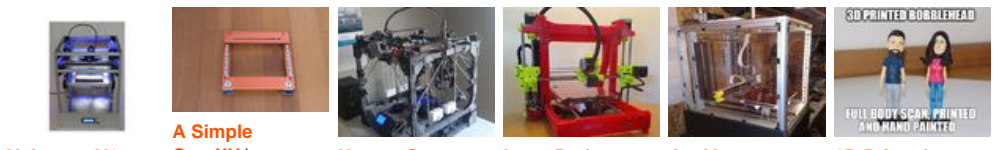
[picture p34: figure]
A Simple

Vulcanus V1
Reprap 3D-Printer 300€ (http://www.instructables.com/id/Vulcanus-V1-3D-Printer/?utm_source=pdf&utm_campaign=related) by
Vulcaman (http://www.instructables.com/member/Vulcaman/?utm_source=pdf&utm_campaign=related)

CoreXY (http://www.instructables.com/id/A-Simple-CoreXY/?utm_source=pdf&utm_campaign=related) by
Ufactory (http://www.instructables.com/member/Ufactory/?utm_source=pdf&utm_campaign=related)

How to Create a
Large 3D Printer
using a Smaller
3D Printer -
"Project Locus" (http://www.instructables.com/id/How-to-Create-a-Large-3D-Printer-using-a-Smaller-3/)
by redhatman (http://www.instructables.com/member/redhatman/?utm_source=pdf&utm_campaign=related)

Long Bed
Printed 3d
Printer (http://www.instructables.com/id/Long-Bed-Printed-3d-Printer/?utm_source=pdf&utm_campaign=related) by
dmserve (http://www.instructables.com/member/dmserve/?utm_source=pdf&utm_campaign=related)

An Almost
Reliable, High
Precision, 3D
Printer: Son of
MegaMax (SoM) (http://www.instructables.com/id/An-Almost-Reliable-High-Precision-3D-Printer-Son-o/)
by Mark Rehorst

3D Printed
Bobblehead -
High Resolution
Full Body
Scanned and
Hand Painted (http://www.instructables.com/id/3D-Printed-Bobblehead-High-Resolution-Full-Body-Sc/) by
luiscarlosrsousa (http://www.instructables.com/member/luiscarlosrsousa/?utm_source=pdf&utm_campaign=related)

Advertisements

## Comments

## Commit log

2020-02-16 add BOM table
2020-02-16 add resources found elsewhere
    [Vulcanus Max 40 3d printer BOM.xlsx]
2020-04-12 added new build files
    [12RODBIGBLOCK.stl, 12RODSMALLBLOCK.stl, CoreXY_Belt_tensioner.stl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]
2021-01-17 updates and new files
    [Vulcanus Max 40 3d printer BOM.xlsx, bed corner 1.stl, bed corner 2.stl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]
2021-03-15 updated marlin 2.0.7.2 config/build
2021-04-05 pid tuning
